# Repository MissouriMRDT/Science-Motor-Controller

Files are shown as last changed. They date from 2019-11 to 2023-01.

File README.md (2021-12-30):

# ScienceMotorController_Hardware
Hardware files for the Science Motor Controller (Science MOCO) board <br/>
The entire science system runs off of the 12V 40A auxillary buck from Powerboard. 
Science MOCO disctributes power to the rest of the science system (heater board and science sensors) in addition to driving brushed DC motors, servos, and solenoids.

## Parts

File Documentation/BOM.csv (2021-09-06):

Id | Designator | Package | Designation | Item Name | Part Number | Manufacturing Part Number | Vendor | Quantity | Cost Per Item | Cost | URL | Comments
1 | U7,U3,U4,U5,U6,U8 | MultiPowerSO_30 | VNH5019A_E | Motor Driver | 45AC7961 | VNH5019ATR-E | Newark | 6 | 7.51 | 46.02 | https://www.newark.com/stmicroelectronics/vnh5019atr-e/motor-driver-aec-q100-multipowerso/dp/45AC7961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
2 | Conn2,Conn1 | Anderson_3_Vertical_Side_by_Side | AndersonPP |  | 1335G1 |  |  | 2 |  | 0 | https://powerwerx.com/anderson-1335g1-printed-circuit-board-vertical
3 | D7,D10,D13,D16,D19,D26 | D_0603_1608Metric_Pad1.05x0.95mm_HandSolder | D_Zener_Small | Zener Diode | SDZT15R5.6CT-ND | SDZT15R5.6? | Digikey | 6 |  | 0 | https://www.digikey.com/en/products/detail/SDZT15R5.6/SDZT15R5.6CT-ND/5726746?itemSeq=346675758
4 | C3,C4,C5,C6,C7,C8 | C_0603_1608Metric_Pad1.05x0.95mm_HandSolder | 33nF | Capacitor | 1276-2044-1-ND | CL10B333KO8NNNC? | Digikey | 6 |  | 0 | https://www.digikey.com/en/products/detail/CL10B333KO8NNNC/1276-2044-1-ND/3890130?itemSeq=346676154
5 | R7,R8,R9,R10,R11,R12,R16,R17,R18,R19,R20,R21,R25,R26,R27,R28,R29,R30,R34,R35,R36,R37,R38,R39,R43,R44,R45,R46,R47,R48,R56,R57,R58,R59,R60,R61 | R_0603_1608Metric_Pad1.05x0.95mm_HandSolder | 1k | Resistor | RHM1.0KDCT-ND | ESR03EZPJ102? | Digikey | 36 | 0.1 | 3.6 | https://www.digikey.com/en/products/detail/rohm-semiconductor/ESR03EZPJ102/1762924
6 | R6,R15,R24,R33,R42,R55 | R_0603_1608Metric_Pad1.05x0.95mm_HandSolder | 10k | Resistor | RHM10KADCT-ND | ESR03EZPF1002? | Digikey | 6 | 0.12 | 0.72 | https://www.digikey.com/en/products/detail/rohm-semiconductor/ESR03EZPF1002/1983753
7 | Conn3,Conn4,Conn5,Conn6,Conn7,Conn12 | Anderson_2_Horizontal_Side_by_Side | AndersonPP |  | 1336G1 |  |  | 6 |  | 0 | https://powerwerx.com/anderson-1336g1-printed-circuit-board-horizontal
8 | Conn8,Conn9,Conn10,Conn11 | MOLEX_SL_02_Vertical | Molex_SL_02 | Connector | WM4800-ND | 0705430001? | Digikey | 4 | 0.74 | 2.96 | https://www.digikey.com/en/products/detail/molex/0705430001/114915?s=N4IgTCBcDaIOoFkAsAOADGgtAOQCIgF0BfIA
9 | Conn13,Conn14 | MOLEX_SL_03_Vertical | Molex_SL_03 | Connector | WM4801-ND | 0705430002? | Digikey | 2 | 0.74 | 1.48 | https://www.digikey.com/en/products/detail/molex/0705430002/114919?s=N4IgTCBcDaIOoFkAsAOADARgLQDkAiIAugL5A
10 | D6 | LED_0603_1608Metric_Pad1.05x0.95mm_HandSolder | Red LED | LED | 160-1447-1-ND | ?LTST-C191KRKT? | Digikey | 1 | 0.26 | 0.26 | https://www.digikey.com/en/products/detail/lite-on-inc/LTST-C191KRKT/386836
11 | D5 | LED_0603_1608Metric_Pad1.05x0.95mm_HandSolder | Yellow LED | LED | 160-1448-1-ND | ?LTST-C191KSKT? | Digikey | 1 | 0.28 | 0.28 | https://www.digikey.com/en/products/detail/lite-on-inc/LTST-C191KSKT/386838
12 | 12VL,3.3VL | LED_0603_1608Metric_Pad1.05x0.95mm_HandSolder | Green LED | LED | 160-1446-1-ND | LTST-C191KGKT | Digikey | 2 | 0.26 | 0.52 | https://www.digikey.com/en/products/detail/lite-on-inc/LTST-C191KGKT/386834
13 | D27,D28,D8,D9,D11,D12,D14,D15,D17,D18,D20,D21,D22,D23,D24,D25 | LED_0603_1608Metric_Pad1.05x0.95mm_HandSolder | Blue LED | LED | 160-1647-1-ND | ?LTST-C191TBKT? | Digikey | 16 | 0.33 | 5.28 | https://www.digikey.com/en/products/detail/lite-on-inc/LTST-C191TBKT/573587
14 | D1 | LED_0603_1608Metric_Pad1.05x0.95mm_HandSolder | Orange LED | LED | 160-1445-1-ND | ?LTST-C191KFKT? | Digikey | 1 | 0.24 | 0.24 | https://www.digikey.com/en/products/detail/lite-on-inc/LTST-C191KFKT/386832
15 | R1,R2 | R_0603_1608Metric_Pad1.05x0.95mm_HandSolder | 1.2k | Resistor | 311-1.2KDTR-ND | RT0603DRD071K2L? | Digikey | 2 | 0.17 | 0.34 | https://www.digikey.com/en/products/detail/yageo/RT0603DRD071K2L/1035462
16 | R4,R5,R51,R52,R53,R54,R3 | R_0603_1608Metric_Pad1.05x0.95mm_HandSolder | 330 | Resistor | 311-330DTR-ND | RT0603DRD07330RL? | Digikey | 7 | 0.17 | 1.19 | https://www.digikey.com/en/products/detail/yageo/RT0603DRD07330RL/1035528
17 | R13,R14,R22,R23,R31,R32,R40,R41,R49,R50,R62,R63 | R_0603_1608Metric_Pad1.05x0.95mm_HandSolder | 1.5k | Resistor | RHM1.5KDCT-ND | ESR03EZPJ152? | Digikey | 12 | 0.1 | 1.2 | https://www.digikey.com/product-detail/en/rohm-semiconductor/ESR03EZPJ152/RHM1.5KDCT-ND/1983780
18 | C1,C2 | C_0603_1608Metric_Pad1.05x0.95mm_HandSolder | 10uF | Capacitor | 1608-1357-1-ND | 0603J0160104KXT? | Digikey | 2 | 0.59 | 1.18 | https://www.digikey.com/en/products/detail/knowles-syfer/0603J0160104KXT/6282146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
19 | U1 | OKI_Horizontal | OKI | 3.3V OKI | 811-3014-ND | OKI-78SR-3.3/1.5-W36H-C | Digikey | 1 | 4.3 | 4.3 | https://www.digikey.com/product-detail/en/diodes-incorporated/AP1509-33SG-13/AP1509-33SGDICT-ND/1301652
20 | U2 | TM4C129E_Launchpad_FULL_THT_BOTTOM | TM4C129E_Launchpad | Tiva Launchpad | 296-44249-ND | EK-TM4C129EXL | Digikey | 1 | 29.99 | 29.99 | https://www.digikey.com/product-detail/en/texas-instruments/EK-TM4C129EXL/296-44249-ND/5764631

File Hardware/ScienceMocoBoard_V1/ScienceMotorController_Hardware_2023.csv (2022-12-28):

Source: | C:\Users\Brink\OneDrive\Documents\GitHub\ScienceMotorController_Hardware\Hardware\ScienceMocoBoard_V1\ScienceMotorController_Hardware_2023.kicad_sch
Date: | 12/28/2022 3:21:48 PM
Tool: | Eeschema (6.0.10)
Generator: | C:\Program Files\KiCad\6.0\bin\scripting\plugins/bom_csv_grouped_by_value.py
Component Count: | 182
Individual Components:
Item | Qty | Reference(s) | Value | LibPart | Footprint | Datasheet | MANUFACTURER | MAXIMUM_PACKAGE_HEIGHT | PARTREV | STANDARD
 |  | AbsEncode1 | Molex_SL_03 | MRDT_Connectors:Molex_SL_03 | MRDT_Connectors:MOLEX_SL_03_Vertical
 |  | AbsEncode2 | Molex_SL_03 | MRDT_Connectors:Molex_SL_03 | MRDT_Connectors:MOLEX_SL_03_Vertical
 |  | AbsEncode3 | Molex_SL_03 | MRDT_Connectors:Molex_SL_03 | MRDT_Connectors:MOLEX_SL_03_Vertical
 |  | AbsEncode4 | Molex_SL_03 | MRDT_Connectors:Molex_SL_03 | MRDT_Connectors:MOLEX_SL_03_Vertical
 |  | C1 | 1u | Device:C | Capacitor_SMD:C_0603_1608Metric | ~
 |  | C2 | 10u | Device:C_Small | Capacitor_SMD:C_0603_1608Metric | ~
 |  | C3 | 1u | Device:C | Capacitor_SMD:C_0603_1608Metric | ~
 |  | C4 | 1u | Device:C | Capacitor_SMD:C_0603_1608Metric | ~
 |  | C5 | 10u | Device:C_Small | Capacitor_SMD:C_0603_1608Metric | ~
 |  | C6 | 1u | Device:C | Capacitor_SMD:C_0603_1608Metric | ~
 |  | C7 | 1u | Device:C | Capacitor_SMD:C_0603_1608Metric | ~
 |  | C8 | 10u | Device:C_Small | Capacitor_SMD:C_0603_1608Metric | ~
 |  | C9 | 1u | Device:C | Capacitor_SMD:C_0603_1608Metric | ~
 |  | C10 | 1u | Device:C | Capacitor_SMD:C_0603_1608Metric | ~
 |  | C11 | 10u | Device:C_Small | Capacitor_SMD:C_0603_1608Metric | ~
 |  | C12 | 1u | Device:C | Capacitor_SMD:C_0603_1608Metric | ~
 |  | C13 | 0.1uF | Device:C | Capacitor_SMD:C_0603_1608Metric_Pad1.08x0.95mm_HandSolder | ~
 |  | Conn1 | Input | MRDT_Connectors:AndersonPP | MRDT_Connectors:Square_Anderson_2_H_Side_By_Side
 |  | Conn2 | Output1 | MRDT_Connectors:AndersonPP | MRDT_Connectors:Square_Anderson_2_H_Side_By_Side
 |  | Conn3 | Output2 | MRDT_Connectors:AndersonPP | MRDT_Connectors:Square_Anderson_2_H_Side_By_Side
 |  | Conn4 | AndersonPP | MRDT_Connectors:AndersonPP | MRDT_Connectors:Square_Anderson_2_H_Side_By_Side
 |  | Conn5 | AndersonPP | MRDT_Connectors:AndersonPP | MRDT_Connectors:Square_Anderson_2_H_Side_By_Side
 |  | Conn6 | AndersonPP | MRDT_Connectors:AndersonPP | MRDT_Connectors:Square_Anderson_2_H_Side_By_Side
 |  | Conn7 | AndersonPP | MRDT_Connectors:AndersonPP | MRDT_Connectors:Square_Anderson_2_H_Side_By_Side
 |  | D1 | Orange | Device:LED_Small | LED_SMD:LED_0603_1608Metric_Pad1.05x0.95mm_HandSolder | ~
 |  | D2 | GREEN | Device:LED_Small | LED_SMD:LED_0603_1608Metric_Pad1.05x0.95mm_HandSolder | ~
 |  | D3 | D_Small | Device:D_Small | LED_SMD:LED_0603_1608Metric_Pad1.05x0.95mm_HandSolder | ~
 |  | D4 | Orange | Device:LED_Small | LED_SMD:LED_0603_1608Metric_Pad1.05x0.95mm_HandSolder | ~
 |  | D5 | GREEN | Device:LED_Small | LED_SMD:LED_0603_1608Metric_Pad1.05x0.95mm_HandSolder | ~
 |  | D6 | D_Small | Device:D_Small | LED_SMD:LED_0603_1608Metric_Pad1.05x0.95mm_HandSolder | ~
 |  | D7 | YELLOW | Device:LED_Small | LED_SMD:LED_0603_1608Metric_Pad1.05x0.95mm_HandSolder | ~
 |  | D8 | YELLOW | Device:LED_Small | LED_SMD:LED_0603_1608Metric_Pad1.05x0.95mm_HandSolder | ~
 |  | D9 | YELLOW | Device:LED_Small | LED_SMD:LED_0603_1608Metric_Pad1.05x0.95mm_HandSolder | ~
 |  | D10 | YELLOW | Device:LED_Small | LED_SMD:LED_0603_1608Metric_Pad1.05x0.95mm_HandSolder | ~
 |  | D11 | D_Small | Device:D_Small | LED_SMD:LED_0603_1608Metric_Pad1.05x0.95mm_HandSolder | ~
 |  | D12 | Orange | Device:LED_Small | LED_SMD:LED_0603_1608Metric_Pad1.05x0.95mm_HandSolder | ~
 |  | D13 | D_Small | Device:D_Small | LED_SMD:LED_0603_1608Metric_Pad1.05x0.95mm_HandSolder | ~
 |  | D14 | Orange | Device:LED_Small | LED_SMD:LED_0603_1608Metric_Pad1.05x0.95mm_HandSolder | ~
 |  | D15 | Orange | Device:LED_Small | LED_SMD:LED_0603_1608Metric_Pad1.05x0.95mm_HandSolder | ~
 |  | D16 | D_Small | Device:D_Small | LED_SMD:LED_0603_1608Metric_Pad1.05x0.95mm_HandSolder | ~
 |  | D17 | Orange | Device:LED_Small | LED_SMD:LED_0603_1608Metric_Pad1.05x0.95mm_HandSolder | ~
 |  | D18 | D_Small | Device:D_Small | LED_SMD:LED_0603_1608Metric_Pad1.05x0.95mm_HandSolder | ~
 |  | D19 | D_Small | Device:D_Small | LED_SMD:LED_0603_1608Metric_Pad1.05x0.95mm_HandSolder | ~
 |  | D20 | Orange | Device:LED_Small | LED_SMD:LED_0603_1608Metric_Pad1.05x0.95mm_HandSolder | ~
 |  | D21 | D_Small | Device:D_Small | LED_SMD:LED_0603_1608Metric_Pad1.05x0.95mm_HandSolder | ~
 |  | D22 | Orange | Device:LED_Small | LED_SMD:LED_0603_1608Metric_Pad1.05x0.95mm_HandSolder | ~
 |  | D23 | YELLOW | Device:LED_Small | LED_SMD:LED_0603_1608Metric_Pad1.05x0.95mm_HandSolder | ~
 |  | D24 | YELLOW | Device:LED_Small | LED_SMD:LED_0603_1608Metric_Pad1.05x0.95mm_HandSolder | ~
 |  | D25 | YELLOW | Device:LED_Small | LED_SMD:LED_0603_1608Metric_Pad1.05x0.95mm_HandSolder | ~
 |  | D26 | YELLOW | Device:LED_Small | LED_SMD:LED_0603_1608Metric_Pad1.05x0.95mm_HandSolder | ~
 |  | D27 | YELLOW | Device:LED_Small | LED_SMD:LED_0603_1608Metric_Pad1.05x0.95mm_HandSolder | ~
 |  | D28 | YELLOW | Device:LED_Small | LED_SMD:LED_0603_1608Metric_Pad1.05x0.95mm_HandSolder | ~
 |  | D29 | YELLOW | Device:LED_Small | LED_SMD:LED_0603_1608Metric_Pad1.05x0.95mm_HandSolder | ~
 |  | D30 | YELLOW | Device:LED_Small | LED_SMD:LED_0603_1608Metric_Pad1.05x0.95mm_HandSolder | ~
 |  | D31 | YELLOW | Device:LED_Small | LED_SMD:LED_0603_1608Metric_Pad1.05x0.95mm_HandSolder | ~
 |  | D32 | Green | Device:LED_Small | LED_SMD:LED_0603_1608Metric_Pad1.05x0.95mm_HandSolder | ~
 |  | DY1 | LED | Device:LED | LED_SMD:LED_0603_1608Metric_Pad1.05x0.95mm_HandSolder | ~
 |  | DY2 | LED | Device:LED | LED_SMD:LED_0603_1608Metric_Pad1.05x0.95mm_HandSolder | ~
 |  | DY3 | LED | Device:LED | LED_SMD:LED_0603_1608Metric_Pad1.05x0.95mm_HandSolder | ~
 |  | DY4 | LED | Device:LED | LED_SMD:LED_0603_1608Metric_Pad1.05x0.95mm_HandSolder | ~
 |  | DY5 | LED | Device:LED | LED_SMD:LED_0603_1608Metric_Pad1.05x0.95mm_HandSolder | ~
 |  | DY6 | LED | Device:LED | LED_SMD:LED_0603_1608Metric_Pad1.05x0.95mm_HandSolder | ~
 |  | DY7 | LED | Device:LED | LED_SMD:LED_0603_1608Metric_Pad1.05x0.95mm_HandSolder | ~
 |  | DY8 | LED | Device:LED | LED_SMD:LED_0603_1608Metric_Pad1.05x0.95mm_HandSolder | ~
 |  | DY9 | LED | Device:LED | LED_SMD:LED_0603_1608Metric_Pad1.05x0.95mm_HandSolder | ~
 |  | DY10 | LED | Device:LED | LED_SMD:LED_0603_1608Metric_Pad1.05x0.95mm_HandSolder | ~
 |  | DY11 | LED | Device:LED | LED_SMD:LED_0603_1608Metric_Pad1.05x0.95mm_HandSolder | ~
 |  | DY12 | LED | Device:LED | LED_SMD:LED_0603_1608Metric_Pad1.05x0.95mm_HandSolder | ~
 |  | J1 | RJ45_LED_Shielded | Connector:RJ45_LED_Shielded | MRDT_Connectors:RJ45_Teensy | ~
 |  | J2 | Conn_02x03_Counter_Clockwise | Connector_Generic:Conn_02x03_Counter_Clockwise | Connector_PinHeader_2.00mm:PinHeader_2x03_P2.00mm_Vertical | ~
 |  | LimSwitch1 | Molex_SL_02 | MRDT_Connectors:Molex_SL_02 | MRDT_Connectors:MOLEX_SL_02_Vertical
 |  | LimSwitch2 | Molex_SL_02 | MRDT_Connectors:Molex_SL_02 | MRDT_Connectors:MOLEX_SL_02_Vertical
 |  | LimSwitch3 | Molex_SL_02 | MRDT_Connectors:Molex_SL_02 | MRDT_Connectors:MOLEX_SL_02_Vertical
 |  | LimSwitch4 | Molex_SL_02 | MRDT_Connectors:Molex_SL_02 | MRDT_Connectors:MOLEX_SL_02_Vertical
 |  | LimSwitch5 | Molex_SL_02 | MRDT_Connectors:Molex_SL_02 | MRDT_Connectors:MOLEX_SL_02_Vertical
 |  | LimSwitch6 | Molex_SL_02 | MRDT_Connectors:Molex_SL_02 | MRDT_Connectors:MOLEX_SL_02_Vertical
 |  | LimSwitch7 | Molex_SL_02 | MRDT_Connectors:Molex_SL_02 | MRDT_Connectors:MOLEX_SL_02_Vertical
 |  | LimSwitch8 | Molex_SL_02 | MRDT_Connectors:Molex_SL_02 | MRDT_Connectors:MOLEX_SL_02_Vertical
 |  | LimSwitch9 | Molex_SL_02 | MRDT_Connectors:Molex_SL_02 | MRDT_Connectors:MOLEX_SL_02_Vertical
 |  | Q1 | SI4156DY | Transistor_FET:FDS2734 | Package_SO:SOIC-8_3.9x4.9mm_P1.27mm | https://www.onsemi.com/pdf/datasheet/fds8896-d.pdf
 |  | Q2 | SI4156DY | Transistor_FET:FDS2734 | Package_SO:SOIC-8_3.9x4.9mm_P1.27mm | https://www.onsemi.com/pdf/datasheet/fds8896-d.pdf
 |  | Q3 | SI4156DY | Transistor_FET:FDS2734 | Package_SO:SOIC-8_3.9x4.9mm_P1.27mm | https://www.onsemi.com/pdf/datasheet/fds8896-d.pdf
 |  | Q4 | SI4156DY | Transistor_FET:FDS2734 | Package_SO:SOIC-8_3.9x4.9mm_P1.27mm | https://www.onsemi.com/pdf/datasheet/fds8896-d.pdf
 |  | Q5 | SI4156DY | Transistor_FET:FDS2734 | Package_SO:SOIC-8_3.9x4.9mm_P1.27mm | https://www.onsemi.com/pdf/datasheet/fds8896-d.pdf
 |  | Q6 | SI4156DY | Transistor_FET:FDS2734 | Package_SO:SOIC-8_3.9x4.9mm_P1.27mm | https://www.onsemi.com/pdf/datasheet/fds8896-d.pdf
 |  | Q7 | SI4156DY | Transistor_FET:FDS2734 | Package_SO:SOIC-8_3.9x4.9mm_P1.27mm | https://www.onsemi.com/pdf/datasheet/fds8896-d.pdf
 |  | Q8 | SI4156DY | Transistor_FET:FDS2734 | Package_SO:SOIC-8_3.9x4.9mm_P1.27mm | https://www.onsemi.com/pdf/datasheet/fds8896-d.pdf
 |  | Q9 | SI4156DY | Transistor_FET:FDS2734 | Package_SO:SOIC-8_3.9x4.9mm_P1.27mm | https://www.onsemi.com/pdf/datasheet/fds8896-d.pdf
 |  | Q10 | SI4156DY | Transistor_FET:FDS2734 | Package_SO:SOIC-8_3.9x4.9mm_P1.27mm | https://www.onsemi.com/pdf/datasheet/fds8896-d.pdf
 |  | Q11 | SI4156DY | Transistor_FET:FDS2734 | Package_SO:SOIC-8_3.9x4.9mm_P1.27mm | https://www.onsemi.com/pdf/datasheet/fds8896-d.pdf
 |  | Q12 | SI4156DY | Transistor_FET:FDS2734 | Package_SO:SOIC-8_3.9x4.9mm_P1.27mm | https://www.onsemi.com/pdf/datasheet/fds8896-d.pdf
 |  | Q13 | SI4156DY | Transistor_FET:FDS2734 | Package_SO:SOIC-8_3.9x4.9mm_P1.27mm | https://www.onsemi.com/pdf/datasheet/fds8896-d.pdf
 |  | Q14 | SI4156DY | Transistor_FET:FDS2734 | Package_SO:SOIC-8_3.9x4.9mm_P1.27mm | https://www.onsemi.com/pdf/datasheet/fds8896-d.pdf
 |  | Q15 | SI4156DY | Transistor_FET:FDS2734 | Package_SO:SOIC-8_3.9x4.9mm_P1.27mm | https://www.onsemi.com/pdf/datasheet/fds8896-d.pdf
 |  | Q16 | SI4156DY | Transistor_FET:FDS2734 | Package_SO:SOIC-8_3.9x4.9mm_P1.27mm | https://www.onsemi.com/pdf/datasheet/fds8896-d.pdf
 |  | R1 | 120 | Device:R_Small | Resistor_SMD:R_0603_1608Metric_Pad0.98x0.95mm_HandSolder | ~
 |  | R2 | 1k | Device:R | Resistor_SMD:R_0603_1608Metric_Pad0.98x0.95mm_HandSolder | ~
 |  | R3 | 100 | Device:R | Resistor_SMD:R_0603_1608Metric_Pad0.98x0.95mm_HandSolder | ~
 |  | R4 | 100 | Device:R | Resistor_SMD:R_0603_1608Metric_Pad0.98x0.95mm_HandSolder | ~
 |  | R5 | 120 | Device:R_Small | Resistor_SMD:R_0603_1608Metric_Pad0.98x0.95mm_HandSolder | ~
 |  | R6 | 300 | Device:R | Resistor_SMD:R_0603_1608Metric_Pad0.98x0.95mm_HandSolder | ~
 |  | R7 | 100 | Device:R | Resistor_SMD:R_0603_1608Metric_Pad0.98x0.95mm_HandSolder | ~
 |  | R8 | 100 | Device:R | Resistor_SMD:R_0603_1608Metric_Pad0.98x0.95mm_HandSolder | ~
 |  | R9 | 100 | Device:R | Resistor_SMD:R_0603_1608Metric_Pad0.98x0.95mm_HandSolder | ~
 |  | R10 | 100 | Device:R | Resistor_SMD:R_0603_1608Metric_Pad0.98x0.95mm_HandSolder | ~
 |  | R11 | 100 | Device:R | Resistor_SMD:R_0603_1608Metric_Pad0.98x0.95mm_HandSolder | ~
 |  | R12 | 100 | Device:R | Resistor_SMD:R_0603_1608Metric_Pad0.98x0.95mm_HandSolder | ~
 |  | R13 | 100 | Device:R | Resistor_SMD:R_0603_1608Metric_Pad0.98x0.95mm_HandSolder | ~
 |  | R14 | 100 | Device:R | Resistor_SMD:R_0603_1608Metric_Pad0.98x0.95mm_HandSolder | ~
 |  | R15 | 100 | Device:R | Resistor_SMD:R_0603_1608Metric_Pad0.98x0.95mm_HandSolder | ~
 |  | R16 | 100 | Device:R | Resistor_SMD:R_0603_1608Metric_Pad0.98x0.95mm_HandSolder | ~
 |  | R17 | 120 | Device:R | Resistor_SMD:R_0603_1608Metric_Pad0.98x0.95mm_HandSolder | ~
 |  | R18 | 120 | Device:R | Resistor_SMD:R_0603_1608Metric_Pad0.98x0.95mm_HandSolder | ~
 |  | R19 | 120 | Device:R | Resistor_SMD:R_0603_1608Metric_Pad0.98x0.95mm_HandSolder | ~
 |  | R20 | 120 | Device:R | Resistor_SMD:R_0603_1608Metric_Pad0.98x0.95mm_HandSolder | ~
 |  | R21 | 120 | Device:R_Small | Resistor_SMD:R_0603_1608Metric_Pad0.98x0.95mm_HandSolder | ~
 |  | R22 | 100 | Device:R | Resistor_SMD:R_0603_1608Metric_Pad0.98x0.95mm_HandSolder | ~
 |  | R23 | 100 | Device:R | Resistor_SMD:R_0603_1608Metric_Pad0.98x0.95mm_HandSolder | ~
 |  | R24 | 100 | Device:R | Resistor_SMD:R_0603_1608Metric_Pad0.98x0.95mm_HandSolder | ~
 |  | R25 | 100 | Device:R | Resistor_SMD:R_0603_1608Metric_Pad0.98x0.95mm_HandSolder | ~
 |  | R26 | 100 | Device:R | Resistor_SMD:R_0603_1608Metric_Pad0.98x0.95mm_HandSolder | ~
 |  | R27 | 100 | Device:R | Resistor_SMD:R_0603_1608Metric_Pad0.98x0.95mm_HandSolder | ~
 |  | R28 | 120 | Device:R_Small | Resistor_SMD:R_0603_1608Metric_Pad0.98x0.95mm_HandSolder | ~
 |  | R29 | 120 | Device:R_Small | Resistor_SMD:R_0603_1608Metric_Pad0.98x0.95mm_HandSolder | ~
 |  | R30 | 100 | Device:R | Resistor_SMD:R_0603_1608Metric_Pad0.98x0.95mm_HandSolder | ~
 |  | R31 | 100 | Device:R | Resistor_SMD:R_0603_1608Metric_Pad0.98x0.95mm_HandSolder | ~
 |  | R32 | 120 | Device:R_Small | Resistor_SMD:R_0603_1608Metric_Pad0.98x0.95mm_HandSolder | ~
 |  | R33 | 100 | Device:R | Resistor_SMD:R_0603_1608Metric_Pad0.98x0.95mm_HandSolder | ~
 |  | R34 | 100 | Device:R | Resistor_SMD:R_0603_1608Metric_Pad0.98x0.95mm_HandSolder | ~
 |  | R35 | 100 | Device:R | Resistor_SMD:R_0603_1608Metric_Pad0.98x0.95mm_HandSolder | ~
 |  | R36 | 100 | Device:R | Resistor_SMD:R_0603_1608Metric_Pad0.98x0.95mm_HandSolder | ~
 |  | R37 | 100 | Device:R | Resistor_SMD:R_0603_1608Metric_Pad0.98x0.95mm_HandSolder | ~
 |  | R38 | 100 | Device:R | Resistor_SMD:R_0603_1608Metric_Pad0.98x0.95mm_HandSolder | ~
 |  | R39 | 120 | Device:R_Small | Resistor_SMD:R_0603_1608Metric_Pad0.98x0.95mm_HandSolder | ~
 |  | R40 | 100 | Device:R | Resistor_SMD:R_0603_1608Metric_Pad0.98x0.95mm_HandSolder | ~
 |  | R41 | 100 | Device:R | Resistor_SMD:R_0603_1608Metric_Pad0.98x0.95mm_HandSolder | ~
 |  | R42 | 120 | Device:R_Small | Resistor_SMD:R_0603_1608Metric_Pad0.98x0.95mm_HandSolder | ~
 |  | R43 | 120 | Device:R | Resistor_SMD:R_0603_1608Metric_Pad0.98x0.95mm_HandSolder | ~
 |  | R44 | 120 | Device:R | Resistor_SMD:R_0603_1608Metric_Pad0.98x0.95mm_HandSolder | ~
 |  | R45 | 120 | Device:R | Resistor_SMD:R_0603_1608Metric_Pad0.98x0.95mm_HandSolder | ~
 |  | R46 | 120 | Device:R | Resistor_SMD:R_0603_1608Metric_Pad0.98x0.95mm_HandSolder | ~
 |  | R47 | 120 | Device:R | Resistor_SMD:R_0603_1608Metric_Pad0.98x0.95mm_HandSolder | ~
 |  | R48 | 120 | Device:R | Resistor_SMD:R_0603_1608Metric_Pad0.98x0.95mm_HandSolder | ~
 |  | R49 | 120 | Device:R | Resistor_SMD:R_0603_1608Metric_Pad0.98x0.95mm_HandSolder | ~
 |  | R50 | 120 | Device:R | Resistor_SMD:R_0603_1608Metric_Pad0.98x0.95mm_HandSolder | ~
 |  | R51 | 120 | Device:R | Resistor_SMD:R_0603_1608Metric_Pad0.98x0.95mm_HandSolder | ~
 |  | R52 | 120 | Device:R | Resistor_SMD:R_0603_1608Metric_Pad0.98x0.95mm_HandSolder | ~
 |  | Servo1 | Molex_SL_03 | MRDT_Connectors:Molex_SL_03 | MRDT_Connectors:MOLEX_SL_03_Vertical
 |  | Servo2 | Molex_SL_03 | MRDT_Connectors:Molex_SL_03 | MRDT_Connectors:MOLEX_SL_03_Vertical
 |  | Servo3 | Molex_SL_03 | MRDT_Connectors:Molex_SL_03 | MRDT_Connectors:MOLEX_SL_03_Vertical
 |  | Servo4 | Molex_SL_03 | MRDT_Connectors:Molex_SL_03 | MRDT_Connectors:MOLEX_SL_03_Vertical
 |  | Servo5 | Molex_SL_03 | MRDT_Connectors:Molex_SL_03 | MRDT_Connectors:MOLEX_SL_03_Vertical
 |  | Servo6 | Molex_SL_03 | MRDT_Connectors:Molex_SL_03 | MRDT_Connectors:MOLEX_SL_03_Vertical
 |  | SW1 | SW_Push | Switch:SW_Push | Button_Switch_SMD:SW_SPST_EVPBF | ~
 |  | SW2 | SW_Push | Switch:SW_Push | Button_Switch_SMD:SW_SPST_EVPBF | ~
 |  | SW3 | SW_Push | Switch:SW_Push | Button_Switch_SMD:SW_SPST_EVPBF | ~
 |  | SW4 | SW_Push | Switch:SW_Push | Button_Switch_SMD:SW_SPST_EVPBF | ~
 |  | SW5 | SW_Push | Switch:SW_Push | Button_Switch_SMD:SW_SPST_EVPBF | ~
 |  | SW6 | SW_Push | Switch:SW_Push | Button_Switch_SMD:SW_SPST_EVPBF | ~
 |  | SW7 | SW_Push | Switch:SW_Push | Button_Switch_SMD:SW_SPST_EVPBF | ~
 |  | SW8 | SW_Push | Switch:SW_Push | Button_Switch_SMD:SW_SPST_EVPBF | ~
 |  | SW9 | SW_Push | Switch:SW_Push | Button_Switch_SMD:SW_SPST_EVPBF | ~
 |  | SW10 | SW_Push | Switch:SW_Push | Button_Switch_SMD:SW_SPST_EVPBF | ~
 |  | SW11 | SW_DPDT_x2 | Switch:SW_DPDT_x2 | Button_Switch_THT:SW_Slide_1P2T_CK_OS102011MS2Q | ~
 |  | U1 | 74LVC2G04 | 74xGxx:74LVC2G04 | Package_TO_SOT_SMD:SOT-23-6_Handsoldering | http://www.ti.com/lit/sg/scyt129e/scyt129e.pdf
 |  | U2 | IRS2005S | Driver_FET:IRS2005S | Package_SO:SOIC-8_3.9x4.9mm_P1.27mm | https://www.infineon.com/dgdl/Infineon-IRS2005S-DS-v02_00-EN.pdf?fileId=5546d462533600a4015364c4246229e1
 |  | U3 | TSR_1-2450 | Regulator_Switching:TSR_1-2450 | Converter_DCDC:Converter_DCDC_TRACO_TSR-1_THT | http://www.tracopower.com/products/tsr1.pdf
 |  | U4 | 74LVC2G04 | 74xGxx:74LVC2G04 | Package_TO_SOT_SMD:SOT-23-6_Handsoldering | http://www.ti.com/lit/sg/scyt129e/scyt129e.pdf
 |  | U5 | IRS2005S | Driver_FET:IRS2005S | Package_SO:SOIC-8_3.9x4.9mm_P1.27mm | https://www.infineon.com/dgdl/Infineon-IRS2005S-DS-v02_00-EN.pdf?fileId=5546d462533600a4015364c4246229e1
 |  | U6 | IRS2005S | Driver_FET:IRS2005S | Package_SO:SOIC-8_3.9x4.9mm_P1.27mm | https://www.infineon.com/dgdl/Infineon-IRS2005S-DS-v02_00-EN.pdf?fileId=5546d462533600a4015364c4246229e1
 |  | U7 | IRS2005S | Driver_FET:IRS2005S | Package_SO:SOIC-8_3.9x4.9mm_P1.27mm | https://www.infineon.com/dgdl/Infineon-IRS2005S-DS-v02_00-EN.pdf?fileId=5546d462533600a4015364c4246229e1
 |  | U8 | 74LVC2G04 | 74xGxx:74LVC2G04 | Package_TO_SOT_SMD:SOT-23-6_Handsoldering | http://www.ti.com/lit/sg/scyt129e/scyt129e.pdf
 |  | U9 | IRS2005S | Driver_FET:IRS2005S | Package_SO:SOIC-8_3.9x4.9mm_P1.27mm | https://www.infineon.com/dgdl/Infineon-IRS2005S-DS-v02_00-EN.pdf?fileId=5546d462533600a4015364c4246229e1
 |  | U10 | 74LVC2G04 | 74xGxx:74LVC2G04 | Package_TO_SOT_SMD:SOT-23-6_Handsoldering | http://www.ti.com/lit/sg/scyt129e/scyt129e.pdf
 |  | U11 | IRS2005S | Driver_FET:IRS2005S | Package_SO:SOIC-8_3.9x4.9mm_P1.27mm | https://www.infineon.com/dgdl/Infineon-IRS2005S-DS-v02_00-EN.pdf?fileId=5546d462533600a4015364c4246229e1
 |  | U12 | IRS2005S | Driver_FET:IRS2005S | Package_SO:SOIC-8_3.9x4.9mm_P1.27mm | https://www.infineon.com/dgdl/Infineon-IRS2005S-DS-v02_00-EN.pdf?fileId=5546d462533600a4015364c4246229e1
 |  | U13 | Teensy4.1_DEV-16771 | MRDT_Shields:Teensy4.1_DEV-16771 | MRDT_Shields:Teensy_4_1 |  | SparkFun Electronics | 4.07mm | 4.1 | Manufacturer recommendations
 |  | U14 | IRS2005S | Driver_FET:IRS2005S | Package_SO:SOIC-8_3.9x4.9mm_P1.27mm | https://www.infineon.com/dgdl/Infineon-IRS2005S-DS-v02_00-EN.pdf?fileId=5546d462533600a4015364c4246229e1
 |  | V1 | Via | MRDT_Drill_Holes:Via | MRDT_Drill_Holes:4_40_Hole_Corner
 |  | V2 | Via | MRDT_Drill_Holes:Via | MRDT_Drill_Holes:4_40_Hole_Corner
 |  | V3 | Via | MRDT_Drill_Holes:Via | MRDT_Drill_Holes:4_40_Hole_Corner
 |  | V4 | Via | MRDT_Drill_Holes:Via | MRDT_Drill_Holes:4_40_Hole_Corner
Collated Components:
Item | Qty | Reference(s) | Value | LibPart | Footprint | Datasheet | MANUFACTURER | MAXIMUM_PACKAGE_HEIGHT | PARTREV | STANDARD
1 | 10 | AbsEncode1, AbsEncode2, AbsEncode3, AbsEncode4, Servo1, Servo2, Servo3, Servo4, Servo5, Servo6 | Molex_SL_03 | MRDT_Connectors:Molex_SL_03 | MRDT_Connectors:MOLEX_SL_03_Vertical
2 | 8 | C1, C3, C4, C6, C7, C9, C10, C12 | 1u | Device:C | Capacitor_SMD:C_0603_1608Metric | ~
3 | 4 | C2, C5, C8, C11 | 10u | Device:C_Small | Capacitor_SMD:C_0603_1608Metric | ~
4 | 1 | C13 | 0.1uF | Device:C | Capacitor_SMD:C_0603_1608Metric_Pad1.08x0.95mm_HandSolder | ~
5 | 1 | Conn1 | Input | MRDT_Connectors:AndersonPP | MRDT_Connectors:Square_Anderson_2_H_Side_By_Side
6 | 1 | Conn2 | Output1 | MRDT_Connectors:AndersonPP | MRDT_Connectors:Square_Anderson_2_H_Side_By_Side
7 | 1 | Conn3 | Output2 | MRDT_Connectors:AndersonPP | MRDT_Connectors:Square_Anderson_2_H_Side_By_Side
8 | 4 | Conn4, Conn5, Conn6, Conn7 | AndersonPP | MRDT_Connectors:AndersonPP | MRDT_Connectors:Square_Anderson_2_H_Side_By_Side
9 | 8 | D1, D4, D12, D14, D15, D17, D20, D22 | Orange | Device:LED_Small | LED_SMD:LED_0603_1608Metric_Pad1.05x0.95mm_HandSolder | ~
10 | 2 | D2, D5 | GREEN | Device:LED_Small | LED_SMD:LED_0603_1608Metric_Pad1.05x0.95mm_HandSolder | ~
11 | 8 | D3, D6, D11, D13, D16, D18, D19, D21 | D_Small | Device:D_Small | LED_SMD:LED_0603_1608Metric_Pad1.05x0.95mm_HandSolder | ~
12 | 13 | D7, D8, D9, D10, D23, D24, D25, D26, D27, D28, D29, D30, D31 | YELLOW | Device:LED_Small | LED_SMD:LED_0603_1608Metric_Pad1.05x0.95mm_HandSolder | ~
13 | 1 | D32 | Green | Device:LED_Small | LED_SMD:LED_0603_1608Metric_Pad1.05x0.95mm_HandSolder | ~
14 | 12 | DY1, DY2, DY3, DY4, DY5, DY6, DY7, DY8, DY9, DY10, DY11, DY12 | LED | Device:LED | LED_SMD:LED_0603_1608Metric_Pad1.05x0.95mm_HandSolder | ~
15 | 1 | J1 | RJ45_LED_Shielded | Connector:RJ45_LED_Shielded | MRDT_Connectors:RJ45_Teensy | ~
16 | 1 | J2 | Conn_02x03_Counter_Clockwise | Connector_Generic:Conn_02x03_Counter_Clockwise | Connector_PinHeader_2.00mm:PinHeader_2x03_P2.00mm_Vertical | ~
17 | 9 | LimSwitch1, LimSwitch2, LimSwitch3, LimSwitch4, LimSwitch5, LimSwitch6, LimSwitch7, LimSwitch8, LimSwitch9 | Molex_SL_02 | MRDT_Connectors:Molex_SL_02 | MRDT_Connectors:MOLEX_SL_02_Vertical
18 | 16 | Q1, Q2, Q3, Q4, Q5, Q6, Q7, Q8, Q9, Q10, Q11, Q12, Q13, Q14, Q15, Q16 | SI4156DY | Transistor_FET:FDS2734 | Package_SO:SOIC-8_3.9x4.9mm_P1.27mm | https://www.onsemi.com/pdf/datasheet/fds8896-d.pdf
19 | 8 | R1, R5, R21, R28, R29, R32, R39, R42 | 120 | Device:R_Small | Resistor_SMD:R_0603_1608Metric_Pad0.98x0.95mm_HandSolder | ~
20 | 1 | R2 | 1k | Device:R | Resistor_SMD:R_0603_1608Metric_Pad0.98x0.95mm_HandSolder | ~
21 | 28 | R3, R4, R7, R8, R9, R10, R11, R12, R13, R14, R15, R16, R22, R23, R24, R25, R26, R27, R30, R31, R33, R34, R35, R36, R37, R38, R40, R41 | 100 | Device:R | Resistor_SMD:R_0603_1608Metric_Pad0.98x0.95mm_HandSolder | ~
22 | 1 | R6 | 300 | Device:R | Resistor_SMD:R_0603_1608Metric_Pad0.98x0.95mm_HandSolder | ~
23 | 14 | R17, R18, R19, R20, R43, R44, R45, R46, R47, R48, R49, R50, R51, R52 | 120 | Device:R | Resistor_SMD:R_0603_1608Metric_Pad0.98x0.95mm_HandSolder | ~
24 | 10 | SW1, SW2, SW3, SW4, SW5, SW6, SW7, SW8, SW9, SW10 | SW_Push | Switch:SW_Push | Button_Switch_SMD:SW_SPST_EVPBF | ~
25 | 1 | SW11 | SW_DPDT_x2 | Switch:SW_DPDT_x2 | Button_Switch_THT:SW_Slide_1P2T_CK_OS102011MS2Q | ~
26 | 4 | U1, U4, U8, U10 | 74LVC2G04 | 74xGxx:74LVC2G04 | Package_TO_SOT_SMD:SOT-23-6_Handsoldering | http://www.ti.com/lit/sg/scyt129e/scyt129e.pdf
27 | 8 | U2, U5, U6, U7, U9, U11, U12, U14 | IRS2005S | Driver_FET:IRS2005S | Package_SO:SOIC-8_3.9x4.9mm_P1.27mm | https://www.infineon.com/dgdl/Infineon-IRS2005S-DS-v02_00-EN.pdf?fileId=5546d462533600a4015364c4246229e1
28 | 1 | U3 | TSR_1-2450 | Regulator_Switching:TSR_1-2450 | Converter_DCDC:Converter_DCDC_TRACO_TSR-1_THT | http://www.tracopower.com/products/tsr1.pdf
29 | 1 | U13 | Teensy4.1_DEV-16771 | MRDT_Shields:Teensy4.1_DEV-16771 | MRDT_Shields:Teensy_4_1 |  | SparkFun Electronics | 4.07mm | 4.1 | Manufacturer recommendations
30 | 4 | V1, V2, V3, V4 | Via | MRDT_Drill_Holes:Via | MRDT_Drill_Holes:4_40_Hole_Corner

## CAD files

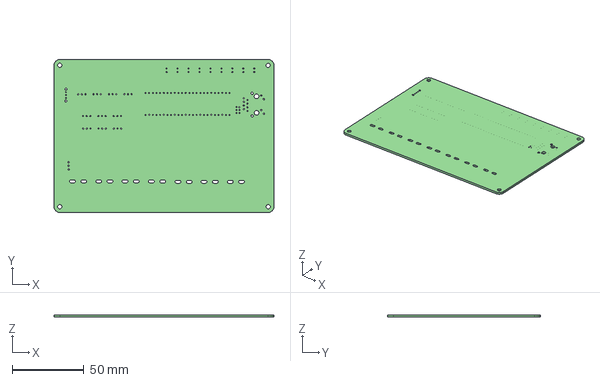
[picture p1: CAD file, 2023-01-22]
Documentation/ScienceMotorController.step
153.0 x 106.4 x 1.60 mm

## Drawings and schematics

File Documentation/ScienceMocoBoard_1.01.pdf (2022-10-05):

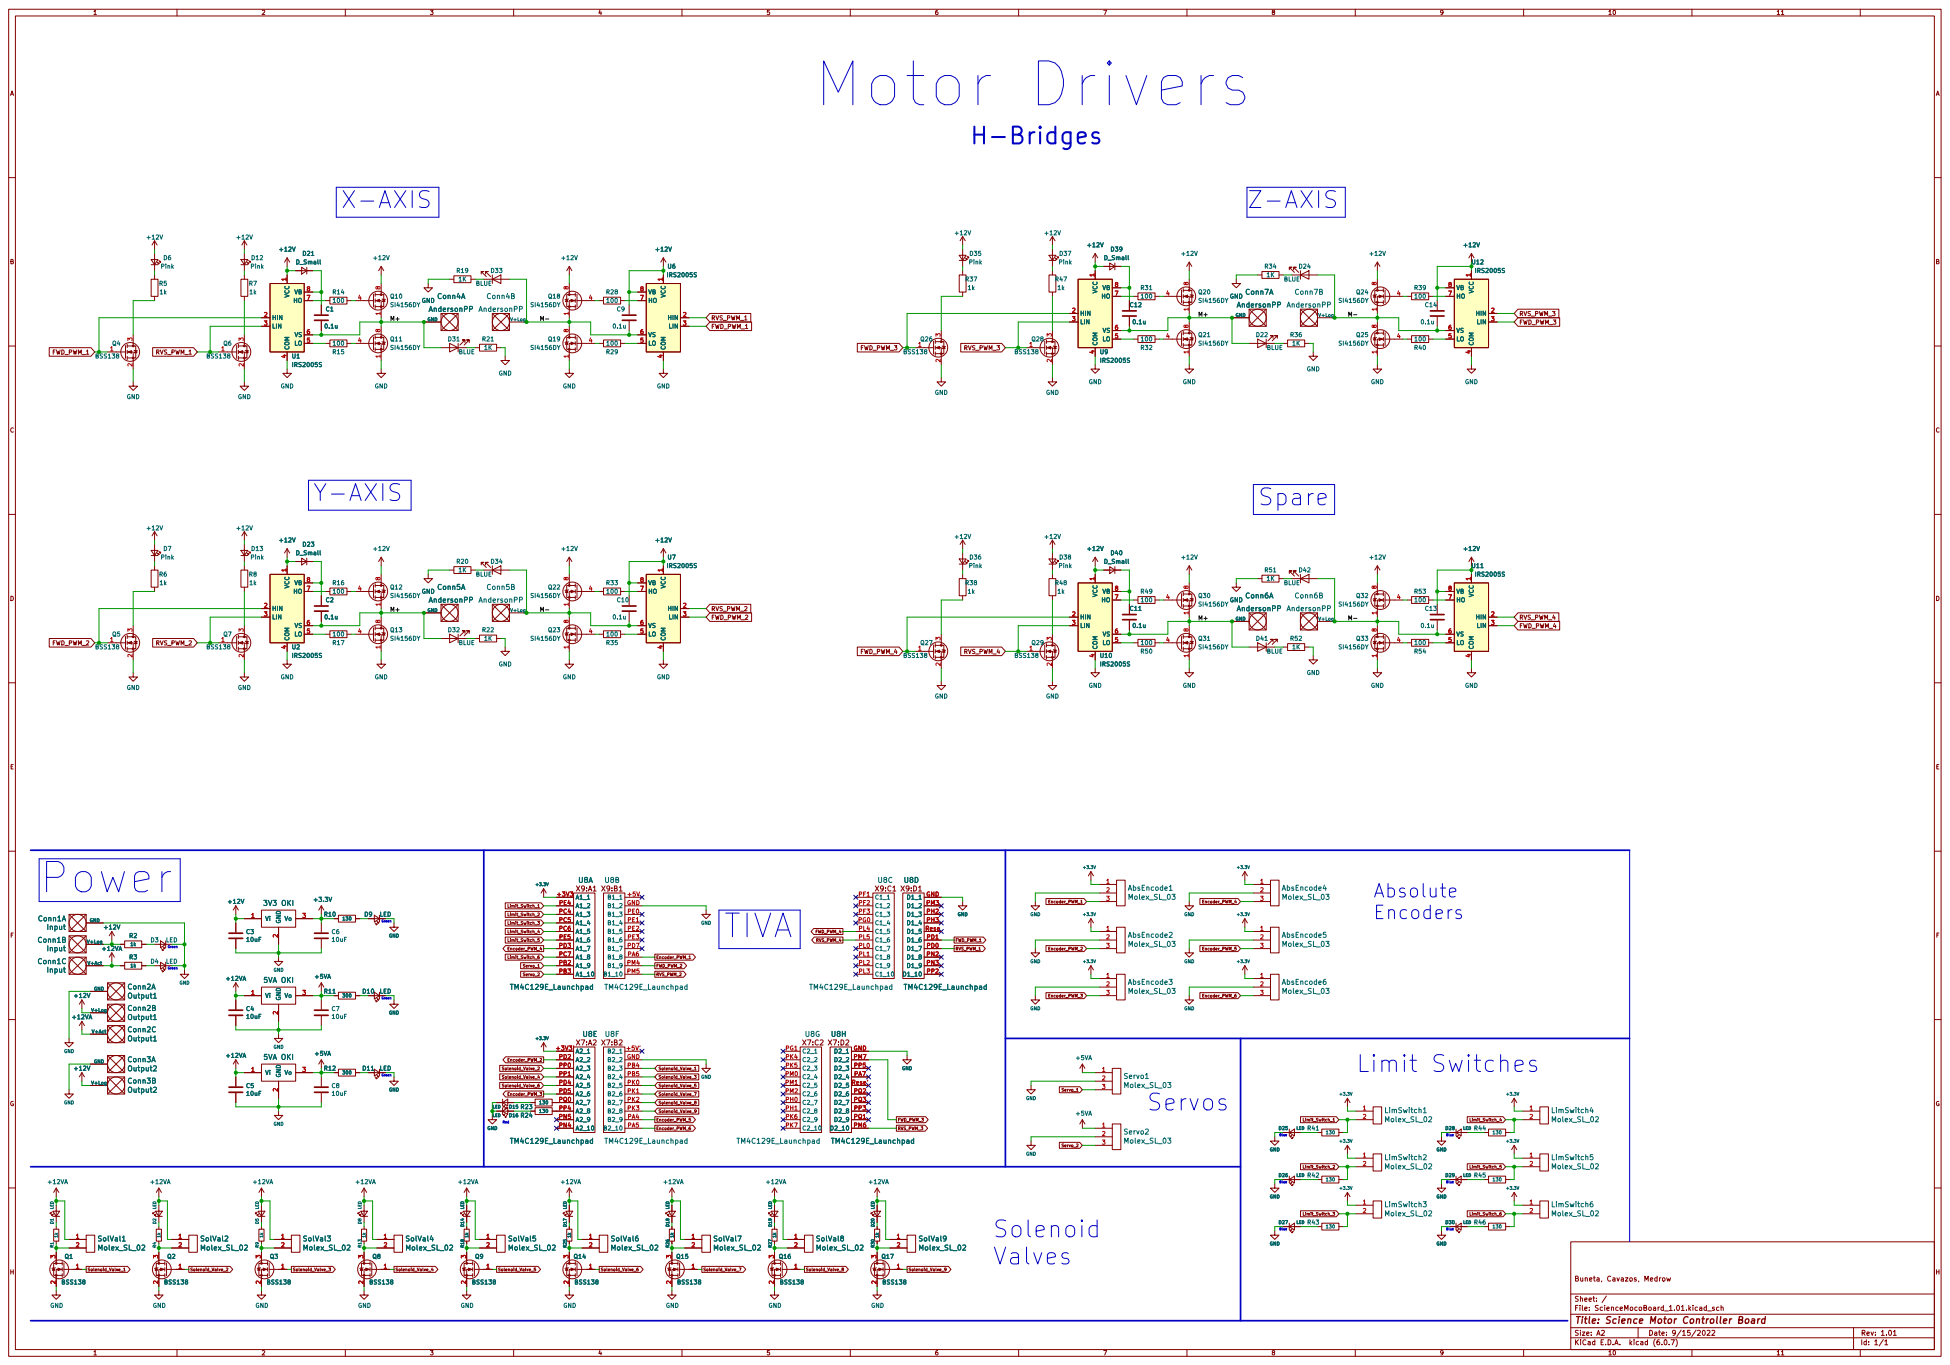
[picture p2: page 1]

Blue Blue Blue Servos

File: ScienceMocoBoard_1.01.kicad_sch Sheet: / Buneta, Cavazos, Medrow

Id: 1/1 Title: Science Motor Controller Board

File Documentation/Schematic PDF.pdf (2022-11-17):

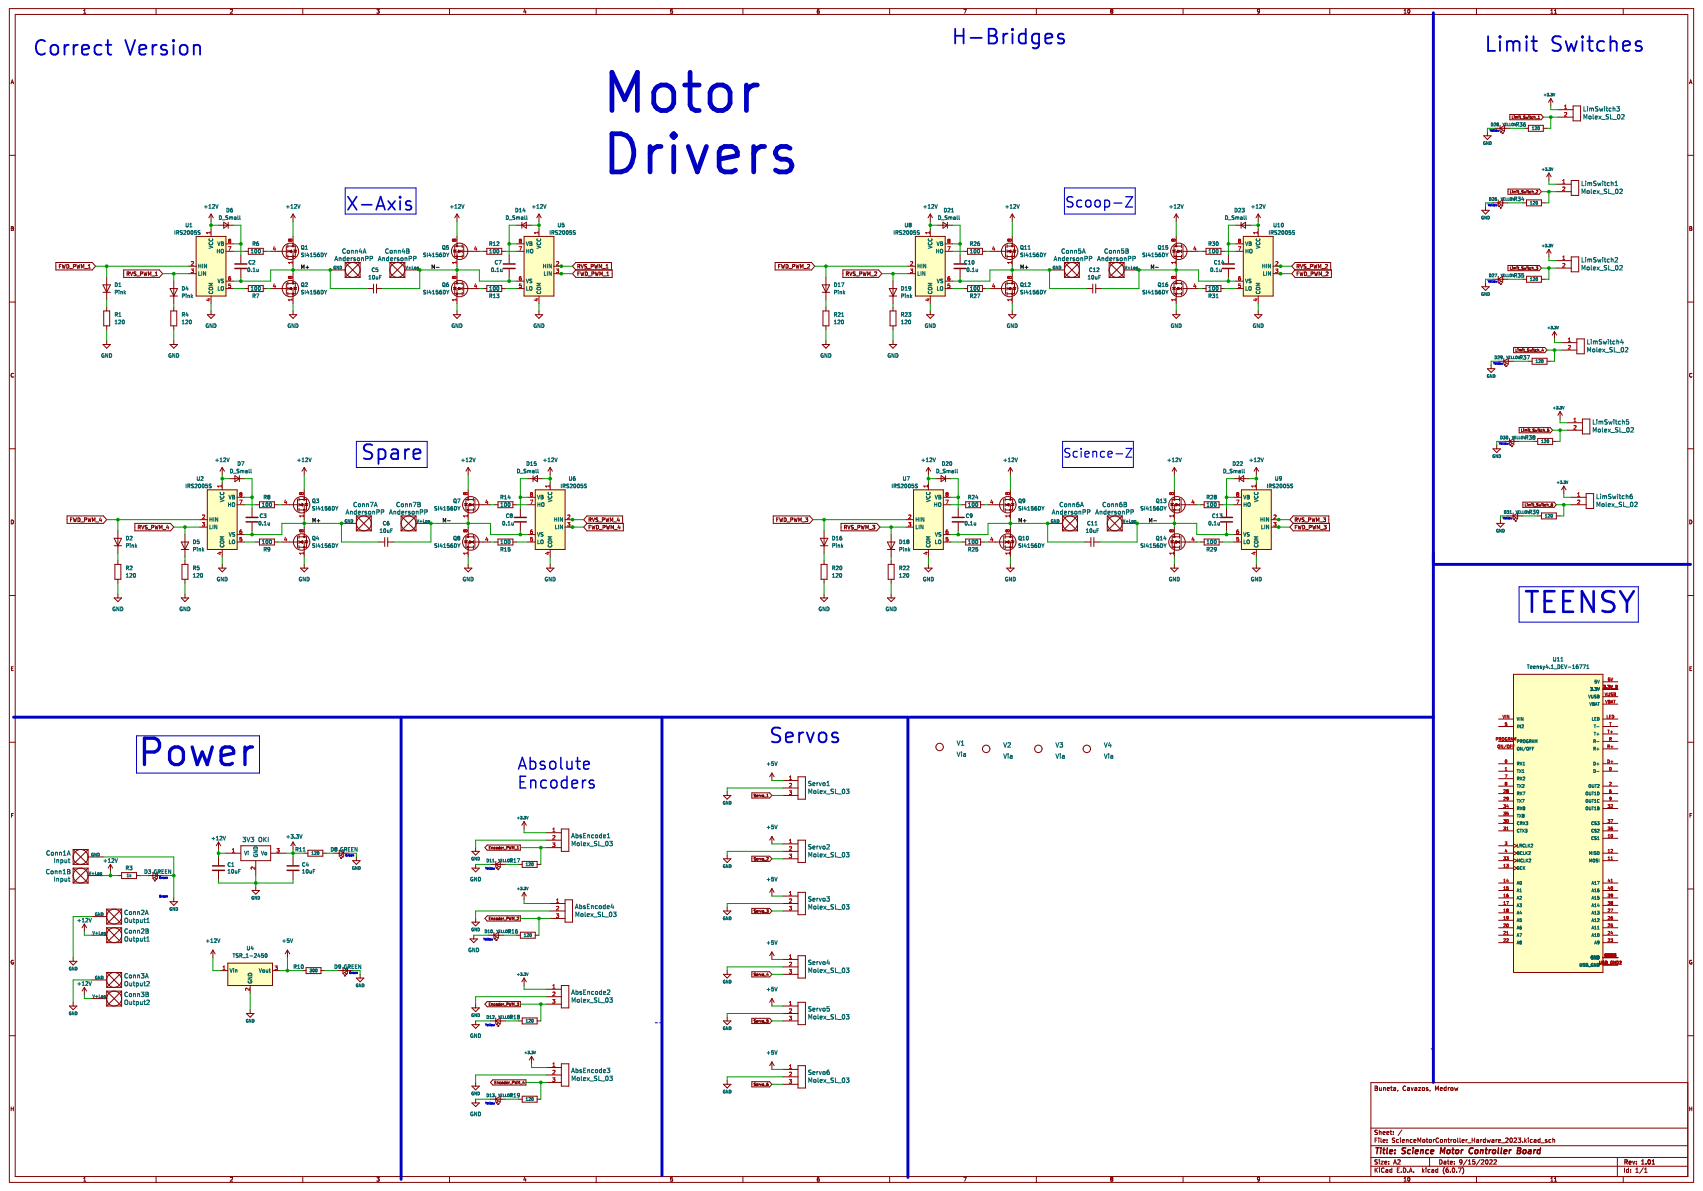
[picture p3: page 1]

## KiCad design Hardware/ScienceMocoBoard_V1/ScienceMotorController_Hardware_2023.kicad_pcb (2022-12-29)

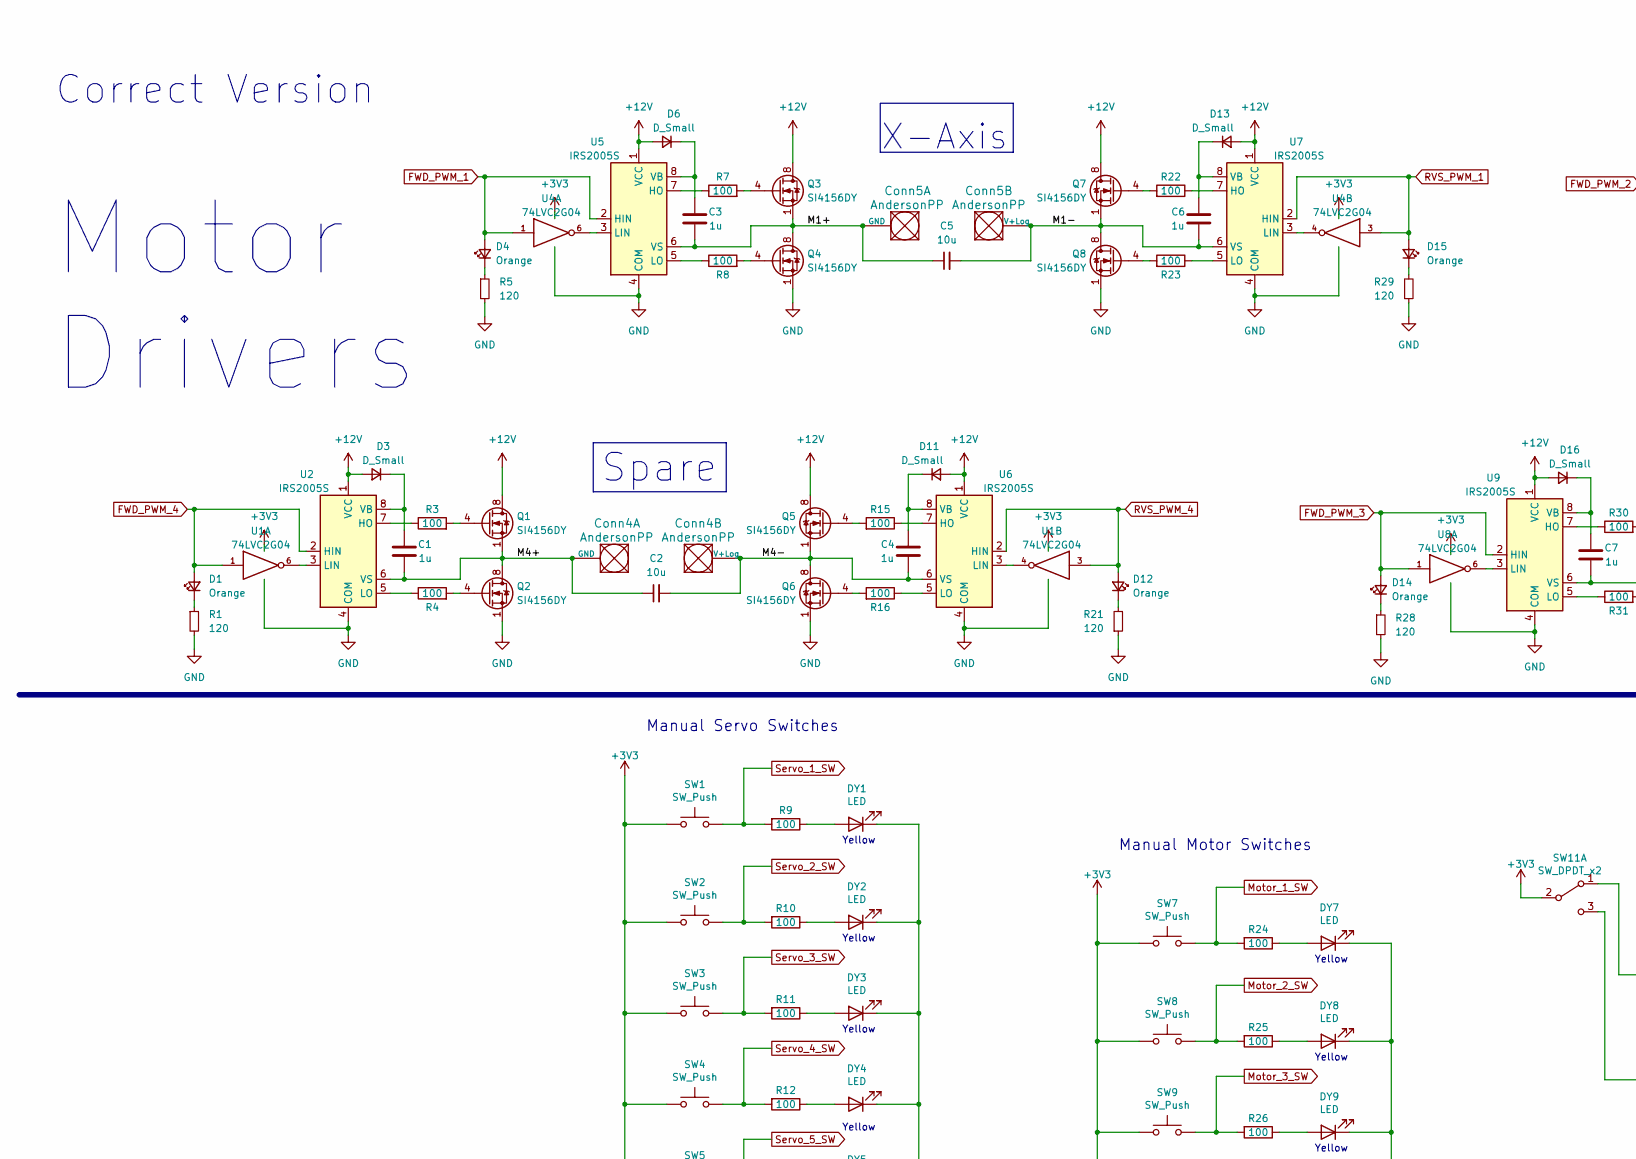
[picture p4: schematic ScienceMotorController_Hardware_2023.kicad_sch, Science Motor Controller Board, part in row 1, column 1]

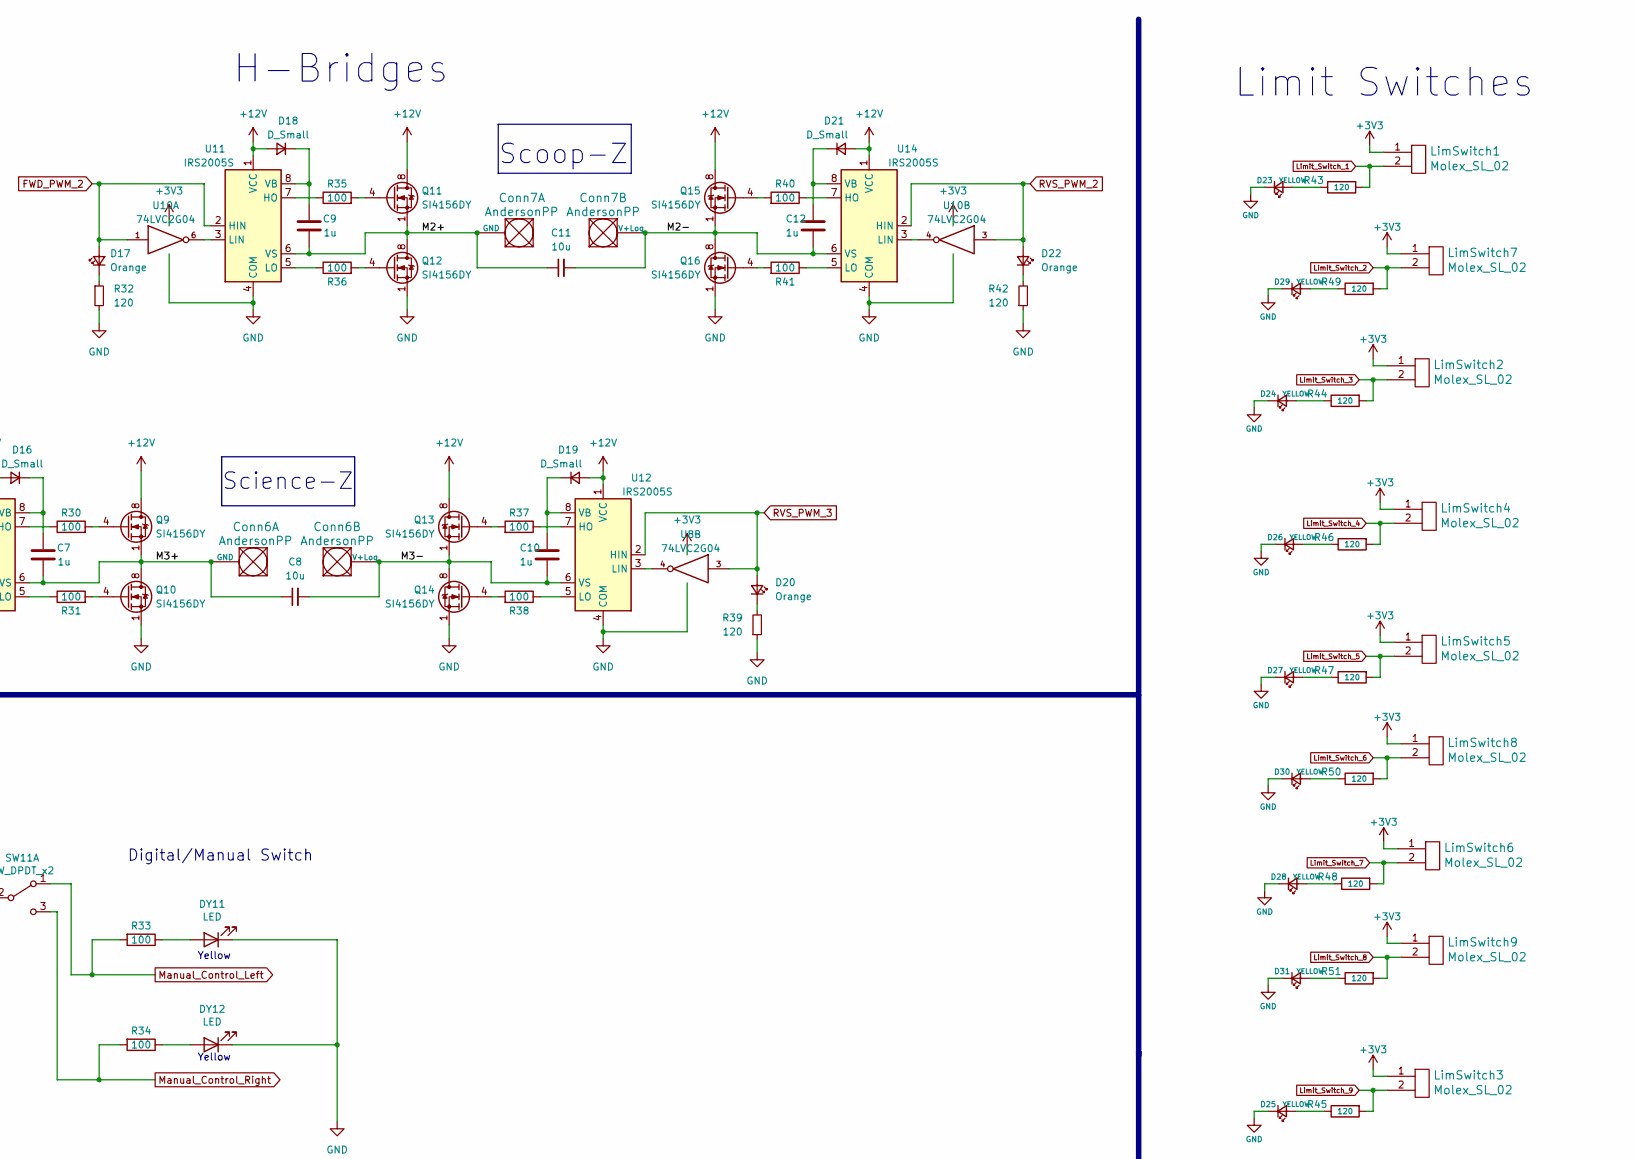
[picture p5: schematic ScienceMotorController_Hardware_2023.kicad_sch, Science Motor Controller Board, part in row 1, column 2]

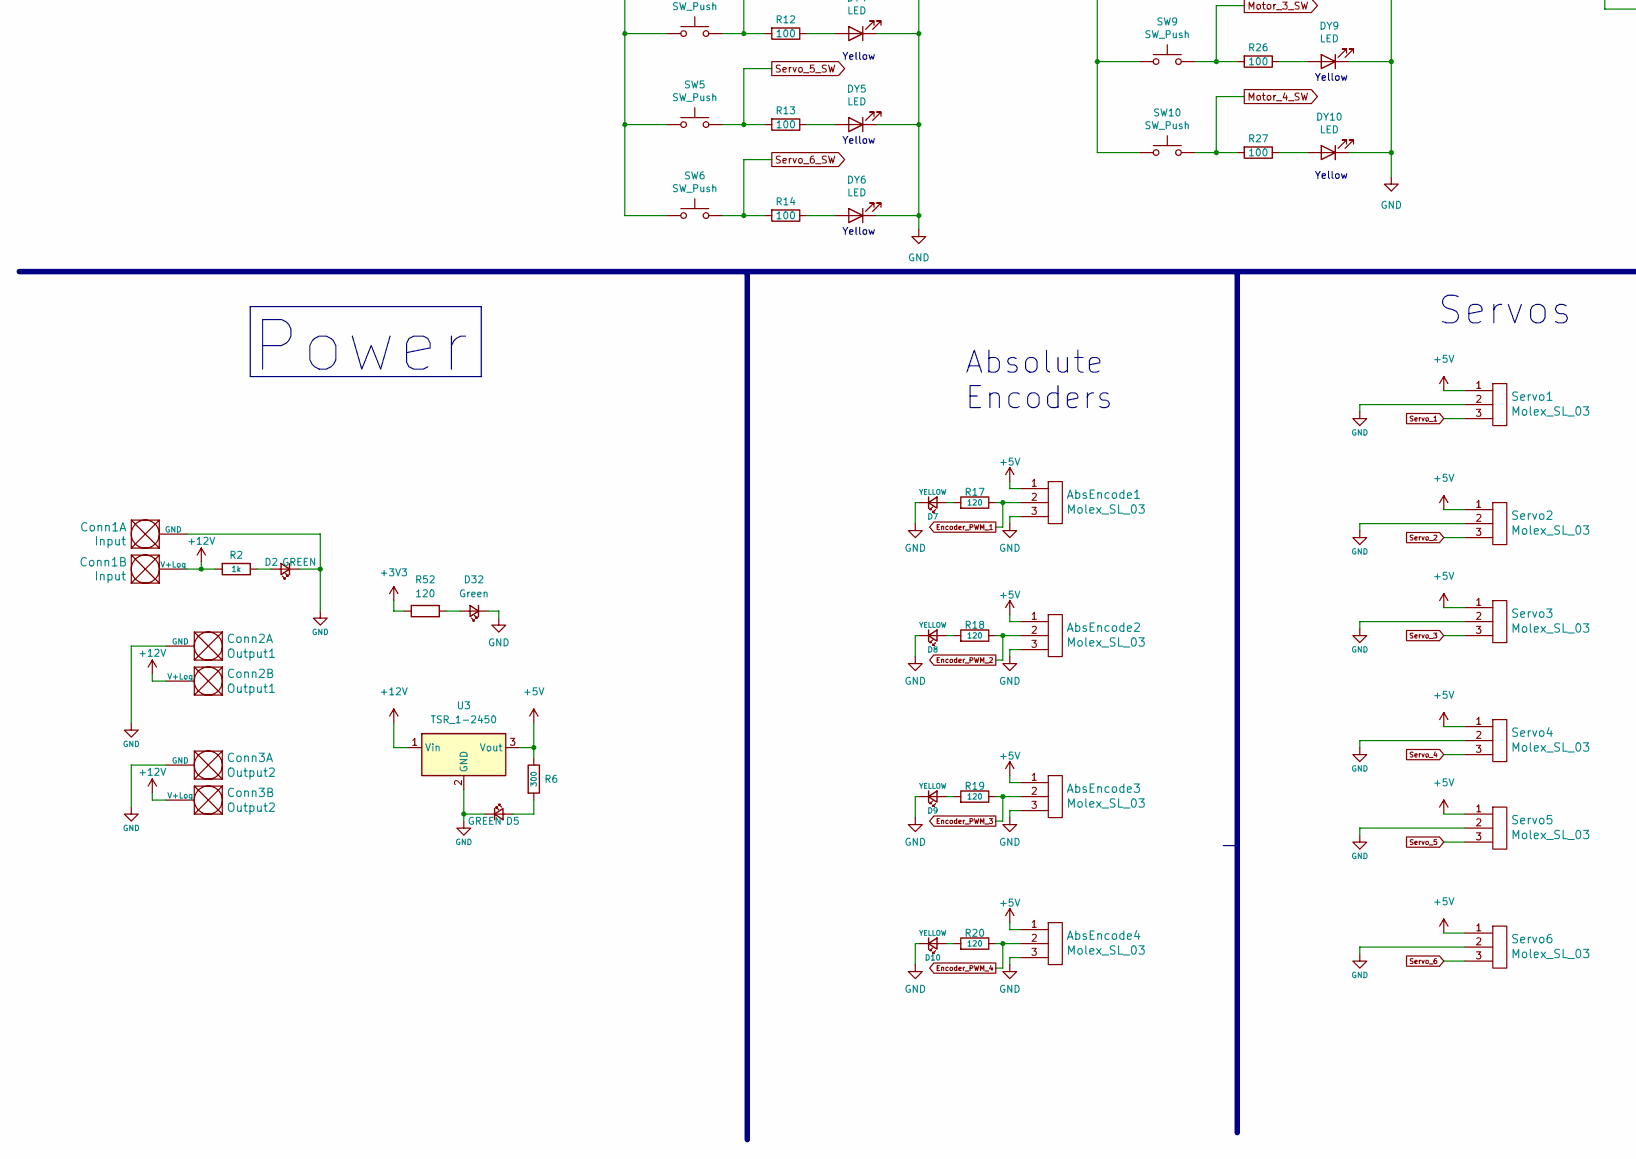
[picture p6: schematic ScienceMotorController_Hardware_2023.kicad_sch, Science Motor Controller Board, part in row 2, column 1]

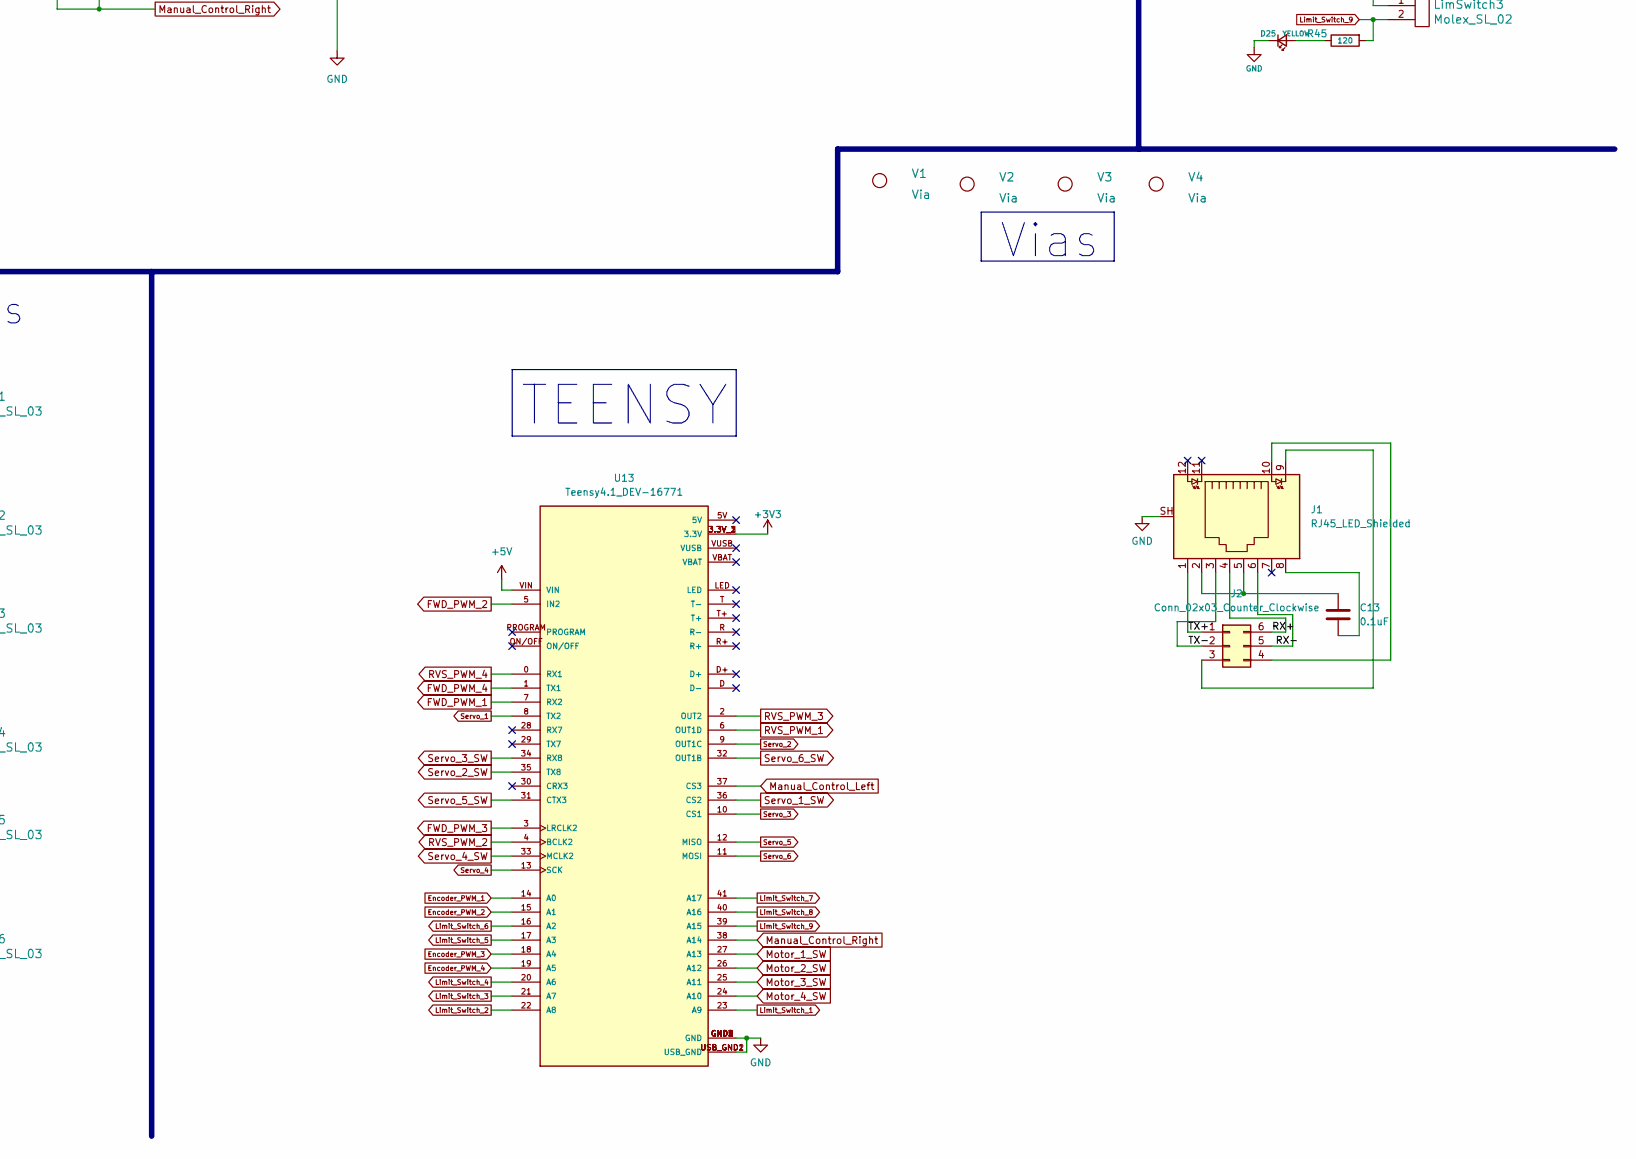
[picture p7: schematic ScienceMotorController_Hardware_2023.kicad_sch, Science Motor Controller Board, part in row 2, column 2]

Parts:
AbsEncode1, AbsEncode2, AbsEncode3, AbsEncode4: Molex_SL_03; MOLEX_SL_03_Vertical
C1, C3, C4, C6, C7, C9, C10, C12: 1u; C_0603_1608Metric
C2, C5, C8, C11: 10u; C_0603_1608Metric
C13: 0.1uF; C_0603_1608Metric_Pad1.08x0.95mm_HandSolder
Conn1: Input; Square_Anderson_2_H_Side_By_Side
Conn2: Output1; Square_Anderson_2_H_Side_By_Side
Conn3: Output2; Square_Anderson_2_H_Side_By_Side
Conn4, Conn5, Conn6, Conn7: AndersonPP; Square_Anderson_2_H_Side_By_Side
D1, D4, D12, D14, D15, D17, D20, D22: Orange; LED_0603_1608Metric_Pad1.05x0.95mm_HandSolder
D2, D5: GREEN; LED_0603_1608Metric_Pad1.05x0.95mm_HandSolder
D3, D6, D11, D13, D16, D18, D19, D21: D_Small; LED_0603_1608Metric_Pad1.05x0.95mm_HandSolder
D7, D8, D9, D10, D23, D24, D25, D26, D27, D28, D29, D30, D31: YELLOW; LED_0603_1608Metric_Pad1.05x0.95mm_HandSolder
D32: Green; LED_0603_1608Metric_Pad1.05x0.95mm_HandSolder
DY1, DY2, DY3, DY4, DY5, DY6, DY7, DY8, DY9, DY10, DY11, DY12: LED; LED_0603_1608Metric_Pad1.05x0.95mm_HandSolder
J1: RJ45_LED_Shielded; RJ45_Teensy
J2: Conn_02x03_Counter_Clockwise; PinHeader_2x03_P2.00mm_Vertical
LimSwitch1, LimSwitch2, LimSwitch3, LimSwitch4, LimSwitch5, LimSwitch6, LimSwitch7, LimSwitch8, LimSwitch9: Molex_SL_02; MOLEX_SL_02_Vertical
Q1, Q2, Q3, Q4, Q5, Q6, Q7, Q8, Q9, Q10, Q11, Q12, Q13, Q14, Q15, Q16: SI4156DY; SOIC-8_3.9x4.9mm_P1.27mm
R1, R5, R17, R18, R19, R20, R21, R28, R29, R32, R39, R42, R43, R44, R45, R46, R47, R48, R49, R50, R51, R52: 120; R_0603_1608Metric_Pad0.98x0.95mm_HandSolder
R2: 1k; R_0603_1608Metric_Pad0.98x0.95mm_HandSolder
R3, R4, R7, R8, R9, R10, R11, R12, R13, R14, R15, R16, R22, R23, R24, R25, R26, R27, R30, R31, R33, R34, R35, R36, R37, R38, R40, R41: 100; R_0603_1608Metric_Pad0.98x0.95mm_HandSolder
R6: 300; R_0603_1608Metric_Pad0.98x0.95mm_HandSolder
SW1, SW2, SW3, SW4, SW5, SW6, SW7, SW8, SW9, SW10: SW_Push; SW_SPST_EVPBF
SW11: SW_DPDT_x2; SW_Slide_1P2T_CK_OS102011MS2Q
Servo1, Servo2, Servo3, Servo4, Servo5, Servo6: Molex_SL_03; MOLEX_SL_03_Vertical
U1, U4, U8, U10: 74LVC2G04; SOT-23-6_Handsoldering
U2, U5, U6, U7, U9, U11, U12, U14: IRS2005S; SOIC-8_3.9x4.9mm_P1.27mm
U3: TSR_1-2450; Converter_DCDC_TRACO_TSR-1_THT
U13: Teensy4.1_DEV-16771; Teensy_4_1_Bare; PARTREV 4.1
V1, V2, V3, V4: Via; 4_40_Hole_Corner

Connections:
+3V3: LimSwitch1.1, LimSwitch2.1, LimSwitch3.1, LimSwitch4.1, LimSwitch5.1, LimSwitch6.1, LimSwitch7.1, LimSwitch8.1, LimSwitch9.1, R52.1, SW1.2, SW2.1, SW3.1, SW4.1, SW5.1, SW6.1, SW7.2, SW8.1, SW9.1, SW10.1, SW11.2 (B), U1.5 (VCC), U4.5 (VCC), U8.5 (VCC), U10.5 (VCC), U13.3.3V_1 (3.3V), U13.3.3V_2 (3.3V), U13.3.3V_3 (3.3V)
+5V: AbsEncode1.1, AbsEncode2.1, AbsEncode3.1, AbsEncode4.1, R6.1, Servo1.1, Servo2.1, Servo3.1, Servo4.1, Servo5.1, Servo6.1, U3.3 (Vout), U13.VIN
+12V: Conn1.2 (V+Log), Conn2.2 (V+Log), Conn3.2 (V+Log), D3.2 (A), D6.2 (A), D11.2 (A), D13.2 (A), D16.2 (A), D18.2 (A), D19.2 (A), D21.2 (A), Q1.5 (D), Q1.6 (D), Q1.7 (D), Q1.8 (D), Q3.5 (D), Q3.6 (D), Q3.7 (D), Q3.8 (D), Q5.5 (D), Q5.6 (D), Q5.7 (D), Q5.8 (D), Q7.5 (D), Q7.6 (D), Q7.7 (D), Q7.8 (D), Q9.5 (D), Q9.6 (D), Q9.7 (D), Q9.8 (D), Q11.5 (D), Q11.6 (D), Q11.7 (D), Q11.8 (D), Q13.5 (D), Q13.6 (D), Q13.7 (D), Q13.8 (D), Q15.5 (D), Q15.6 (D), Q15.7 (D), Q15.8 (D), R2.2, U2.1 (VCC), U3.1 (Vin), U5.1 (VCC), U6.1 (VCC), U7.1 (VCC), U9.1 (VCC), U11.1 (VCC), U12.1 (VCC), U14.1 (VCC)
/M1+: C3.2, C5.1, Conn5.1 (GND), Q3.1 (S), Q3.2 (S), Q3.3 (S), Q4.5 (D), Q4.6 (D), Q4.7 (D), Q4.8 (D), U5.6 (VS)
/M1-: C5.2, C6.2, Conn5.2 (V+Log), Q7.1 (S), Q7.2 (S), Q7.3 (S), Q8.5 (D), Q8.6 (D), Q8.7 (D), Q8.8 (D), U7.6 (VS)
/M2+: C9.2, C11.1, Conn7.1 (GND), Q11.1 (S), Q11.2 (S), Q11.3 (S), Q12.5 (D), Q12.6 (D), Q12.7 (D), Q12.8 (D), U11.6 (VS)
/M2-: C11.2, C12.2, Conn7.2 (V+Log), Q15.1 (S), Q15.2 (S), Q15.3 (S), Q16.5 (D), Q16.6 (D), Q16.7 (D), Q16.8 (D), U14.6 (VS)
/M3+: C7.2, C8.1, Conn6.1 (GND), Q9.1 (S), Q9.2 (S), Q9.3 (S), Q10.5 (D), Q10.6 (D), Q10.7 (D), Q10.8 (D), U9.6 (VS)
/M3-: C8.2, C10.2, Conn6.2 (V+Log), Q13.1 (S), Q13.2 (S), Q13.3 (S), Q14.5 (D), Q14.6 (D), Q14.7 (D), Q14.8 (D), U12.6 (VS)
/M4+: C1.2, C2.1, Conn4.1 (GND), Q1.1 (S), Q1.2 (S), Q1.3 (S), Q2.5 (D), Q2.6 (D), Q2.7 (D), Q2.8 (D), U2.6 (VS)
/M4-: C2.2, C4.2, Conn4.2 (V+Log), Q5.1 (S), Q5.2 (S), Q5.3 (S), Q6.5 (D), Q6.6 (D), Q6.7 (D), Q6.8 (D), U6.6 (VS)
/RX+: J1.4, J2.6
/RX-: J1.6, J2.5
/TX+: J1.1, J2.1
/TX-: J1.3, J2.2
Encoder_PWM_1: AbsEncode1.2, R17.1, U13.14 (A0)
Encoder_PWM_2: AbsEncode2.2, R18.1, U13.15 (A1)
Encoder_PWM_3: AbsEncode3.2, R19.1, U13.18 (A4)
Encoder_PWM_4: AbsEncode4.2, R20.1, U13.19 (A5)
FWD_PWM_1: D4.2 (A), U4.1, U5.2 (HIN), U13.7 (RX2)
FWD_PWM_2: D17.2 (A), U10.1, U11.2 (HIN), U13.5 (IN2)
FWD_PWM_3: D14.2 (A), U8.1, U9.2 (HIN), U13.3 (LRCLK2)
FWD_PWM_4: D1.2 (A), U1.1, U2.2 (HIN), U13.1 (TX1)
GND: AbsEncode1.3, AbsEncode2.3, AbsEncode3.3, AbsEncode4.3, Conn1.1 (GND), Conn2.1 (GND), Conn3.1 (GND), D2.1 (K), D5.1 (K), D7.1 (K), D8.1 (K), D9.1 (K), D10.1 (K), D23.1 (K), D24.1 (K), D25.1 (K), D26.1 (K), D27.1 (K), D28.1 (K), D29.1 (K), D30.1 (K), D31.1 (K), D32.1 (K), DY1.1 (K), DY2.1 (K), DY3.1 (K), DY4.1 (K), DY5.1 (K), DY6.1 (K), DY7.1 (K), DY8.1 (K), DY9.1 (K), DY10.1 (K), DY11.1 (K), DY12.1 (K), J1.SH, Q2.1 (S), Q2.2 (S), Q2.3 (S), Q4.1 (S), Q4.2 (S), Q4.3 (S), Q6.1 (S), Q6.2 (S), Q6.3 (S), Q8.1 (S), Q8.2 (S), Q8.3 (S), Q10.1 (S), Q10.2 (S), Q10.3 (S), Q12.1 (S), Q12.2 (S), Q12.3 (S), Q14.1 (S), Q14.2 (S), Q14.3 (S), Q16.1 (S), Q16.2 (S), Q16.3 (S), R1.2, R5.2, R21.1, R28.2, R29.1, R32.2, R39.1, R42.1, Servo1.2, Servo2.2, Servo3.2, Servo4.2, Servo5.2, Servo6.2, U1.2 (GND), U2.4 (COM), U3.2 (GND), U4.2 (GND), U5.4 (COM), U6.4 (COM), U7.4 (COM), U8.2 (GND), U9.4 (COM), U10.2 (GND), U11.4 (COM), U12.4 (COM), U13.GND1 (GND), U13.GND2 (GND), U13.GND3 (GND), U13.GND4 (GND), U13.GND5 (GND), U13.USB_GND1 (USB_GND), U13.USB_GND2 (USB_GND), U14.4 (COM)
Limit_Switch_1: LimSwitch1.2, R43.2, U13.23 (A9)
Limit_Switch_2: LimSwitch7.2, R49.2, U13.22 (A8)
Limit_Switch_3: LimSwitch2.2, R44.2, U13.21 (A7)
Limit_Switch_4: LimSwitch4.2, R46.2, U13.20 (A6)
Limit_Switch_5: LimSwitch5.2, R47.2, U13.17 (A3)
Limit_Switch_6: LimSwitch8.2, R50.2, U13.16 (A2)
Limit_Switch_7: LimSwitch6.2, R48.2, U13.41 (A17)
Limit_Switch_8: LimSwitch9.2, R51.2, U13.40 (A16)
Limit_Switch_9: LimSwitch3.2, R45.2, U13.39 (A15)
Manual_Control_Left: R33.2, SW11.1 (A), U13.37 (CS3)
Manual_Control_Right: R34.2, SW11.3 (C), U13.38 (A14)
Motor_1_SW: R24.2, SW7.1, U13.27 (A13)
Motor_2_SW: R25.2, SW8.2, U13.26 (A12)
Motor_3_SW: R26.2, SW9.2, U13.25 (A11)
Motor_4_SW: R27.2, SW10.2, U13.24 (A10)
unnamed: C1.1, D3.1 (K), U2.8 (VB)
unnamed: C3.1, D6.1 (K), U5.8 (VB)
unnamed: C4.1, D11.1 (K), U6.8 (VB)
unnamed: C6.1, D13.1 (K), U7.8 (VB)
unnamed: C7.1, D16.1 (K), U9.8 (VB)
unnamed: C9.1, D18.1 (K), U11.8 (VB)
unnamed: C10.1, D19.1 (K), U12.8 (VB)
unnamed: C12.1, D21.1 (K), U14.8 (VB)
unnamed: C13.1, J1.2, J1.5
unnamed: C13.2, J1.8
unnamed: D1.1 (K), R1.1
unnamed: D2.2 (A), R2.1
unnamed: D4.1 (K), R5.1
unnamed: D5.2 (A), R6.2
unnamed: D7.2 (A), R17.2
unnamed: D8.2 (A), R18.2
unnamed: D9.2 (A), R19.2
unnamed: D10.2 (A), R20.2
unnamed: D12.1 (K), R21.2
unnamed: D14.1 (K), R28.1
unnamed: D15.1 (K), R29.2
unnamed: D17.1 (K), R32.1
unnamed: D20.1 (K), R39.2
unnamed: D22.1 (K), R42.2
unnamed: D23.2 (A), R43.1
unnamed: D24.2 (A), R44.1
unnamed: D25.2 (A), R45.1
unnamed: D26.2 (A), R46.1
unnamed: D27.2 (A), R47.1
unnamed: D28.2 (A), R48.1
unnamed: D29.2 (A), R49.1
unnamed: D30.2 (A), R50.1
unnamed: D31.2 (A), R51.1
unnamed: D32.2 (A), R52.2
unnamed: DY1.2 (A), R9.1
unnamed: DY2.2 (A), R10.1
unnamed: DY3.2 (A), R11.1
unnamed: DY4.2 (A), R12.1
unnamed: DY5.2 (A), R13.1
unnamed: DY6.2 (A), R14.1
unnamed: DY7.2 (A), R24.1
unnamed: DY8.2 (A), R25.1
unnamed: DY9.2 (A), R26.1
unnamed: DY10.2 (A), R27.1
unnamed: DY11.2 (A), R33.1
unnamed: DY12.2 (A), R34.1
unnamed: J1.9, J2.3
unnamed: J1.10, J2.4
unnamed: Q1.4 (G), R3.2
unnamed: Q2.4 (G), R4.2
unnamed: Q3.4 (G), R7.2
unnamed: Q4.4 (G), R8.2
unnamed: Q5.4 (G), R15.2
unnamed: Q6.4 (G), R16.2
unnamed: Q7.4 (G), R22.2
unnamed: Q8.4 (G), R23.2
unnamed: Q9.4 (G), R30.2
unnamed: Q10.4 (G), R31.2
unnamed: Q11.4 (G), R35.2
unnamed: Q12.4 (G), R36.2
unnamed: Q13.4 (G), R37.2
unnamed: Q14.4 (G), R38.2
unnamed: Q15.4 (G), R40.2
unnamed: Q16.4 (G), R41.2
unnamed: R3.1, U2.7 (HO)
unnamed: R4.1, U2.5 (LO)
unnamed: R7.1, U5.7 (HO)
unnamed: R8.1, U5.5 (LO)
unnamed: R15.1, U6.7 (HO)
unnamed: R16.1, U6.5 (LO)
unnamed: R22.1, U7.7 (HO)
unnamed: R23.1, U7.5 (LO)
unnamed: R30.1, U9.7 (HO)
unnamed: R31.1, U9.5 (LO)
unnamed: R35.1, U11.7 (HO)
unnamed: R36.1, U11.5 (LO)
unnamed: R37.1, U12.7 (HO)
unnamed: R38.1, U12.5 (LO)
unnamed: R40.1, U14.7 (HO)
unnamed: R41.1, U14.5 (LO)
unnamed: U1.4, U6.3 (LIN)
unnamed: U1.6, U2.3 (LIN)
unnamed: U4.4, U7.3 (LIN)
unnamed: U4.6, U5.3 (LIN)
unnamed: U8.6, U9.3 (LIN)
unnamed: U10.4, U14.3 (LIN)
unnamed: U10.6, U11.3 (LIN)
unnamed: U8.4, U12.3 (LIN)
RVS_PWM_1: D15.2 (A), U4.3, U7.2 (HIN), U13.6 (OUT1D)
RVS_PWM_2: D22.2 (A), U10.3, U13.4 (BCLK2), U14.2 (HIN)
RVS_PWM_3: D20.2 (A), U8.3, U12.2 (HIN), U13.2 (OUT2)
RVS_PWM_4: D12.2 (A), U1.3, U6.2 (HIN), U13.0 (RX1)
Servo_1: Servo1.3, U13.8 (TX2)
Servo_1_SW: R9.2, SW1.1, U13.36 (CS2)
Servo_2: Servo2.3, U13.9 (OUT1C)
Servo_2_SW: R10.2, SW2.2, U13.35 (TX8)
Servo_3: Servo3.3, U13.10 (CS1)
Servo_3_SW: R11.2, SW3.2, U13.34 (RX8)
Servo_4: Servo4.3, U13.13 (SCK)
Servo_4_SW: R12.2, SW4.2, U13.33 (MCLK2)
Servo_5: Servo5.3, U13.12 (MISO)
Servo_5_SW: R13.2, SW5.2, U13.31 (CTX3)
Servo_6: Servo6.3, U13.11 (MOSI)
Servo_6_SW: R14.2, SW6.2, U13.32 (OUT1B)

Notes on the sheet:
Yellow
TEENSY
X-Axis
Power
Absolute Encoders
Motor Drivers
Vias
Spare
Correct Version
Manual Servo Switches
Limit Switches
Servos
Science-Z
Manual Motor Switches
H-Bridges
Scoop-Z
Digital/Manual Switch

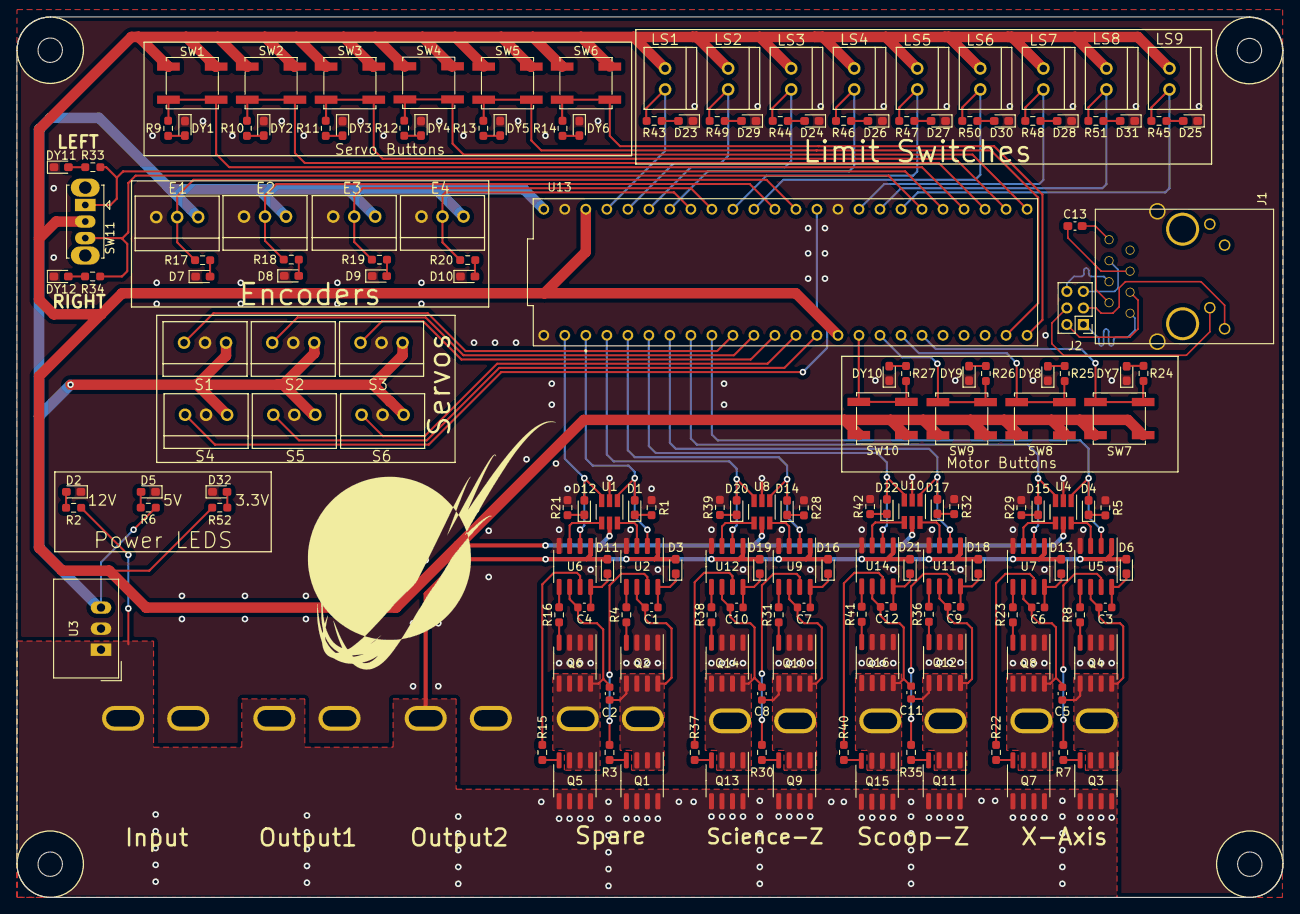
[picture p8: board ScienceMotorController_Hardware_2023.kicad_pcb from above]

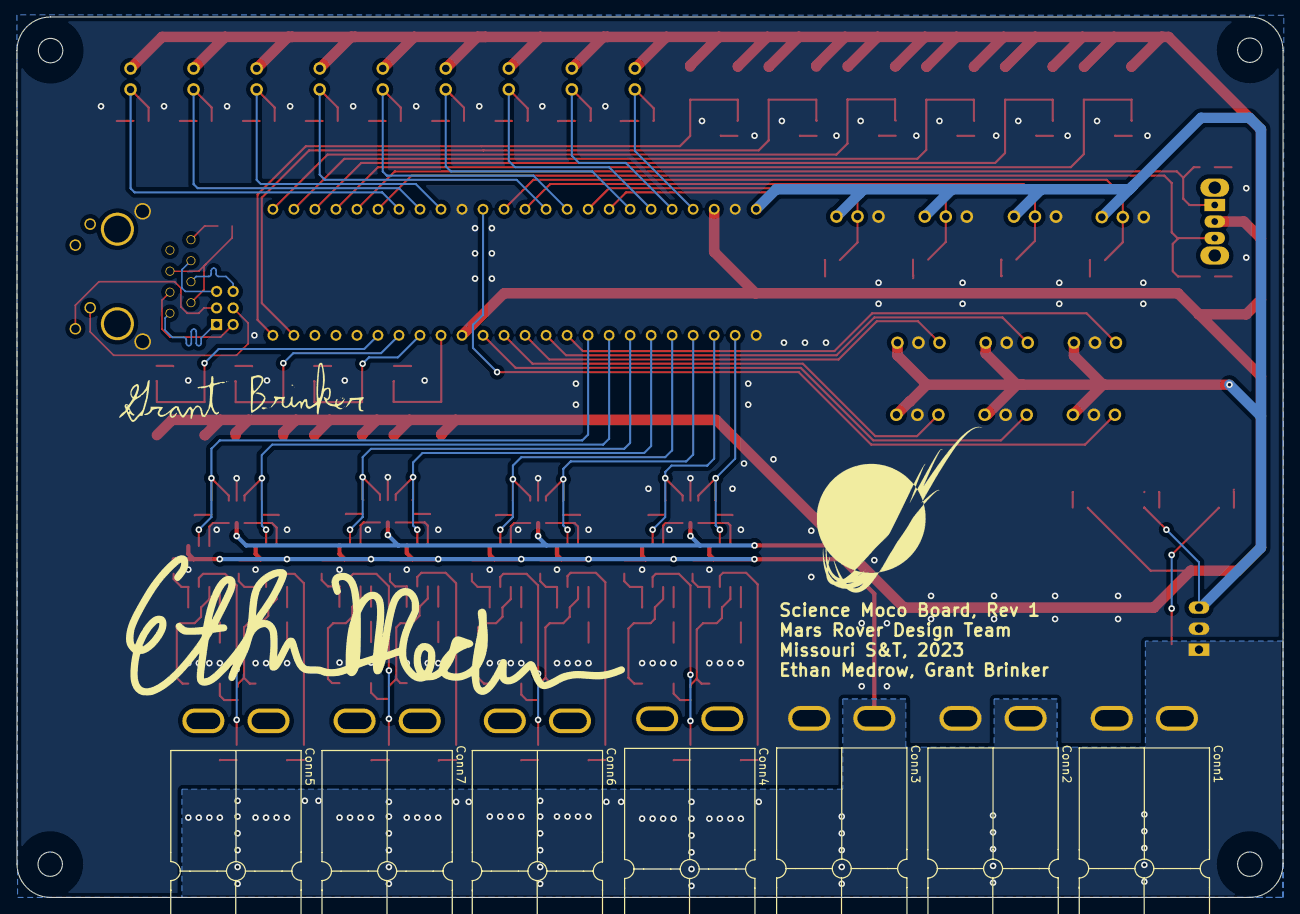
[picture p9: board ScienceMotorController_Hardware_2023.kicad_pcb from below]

Board: 2 copper layers, 153.0 x 106.4 mm, 182 parts (7 on the bottom side), 143 nets.

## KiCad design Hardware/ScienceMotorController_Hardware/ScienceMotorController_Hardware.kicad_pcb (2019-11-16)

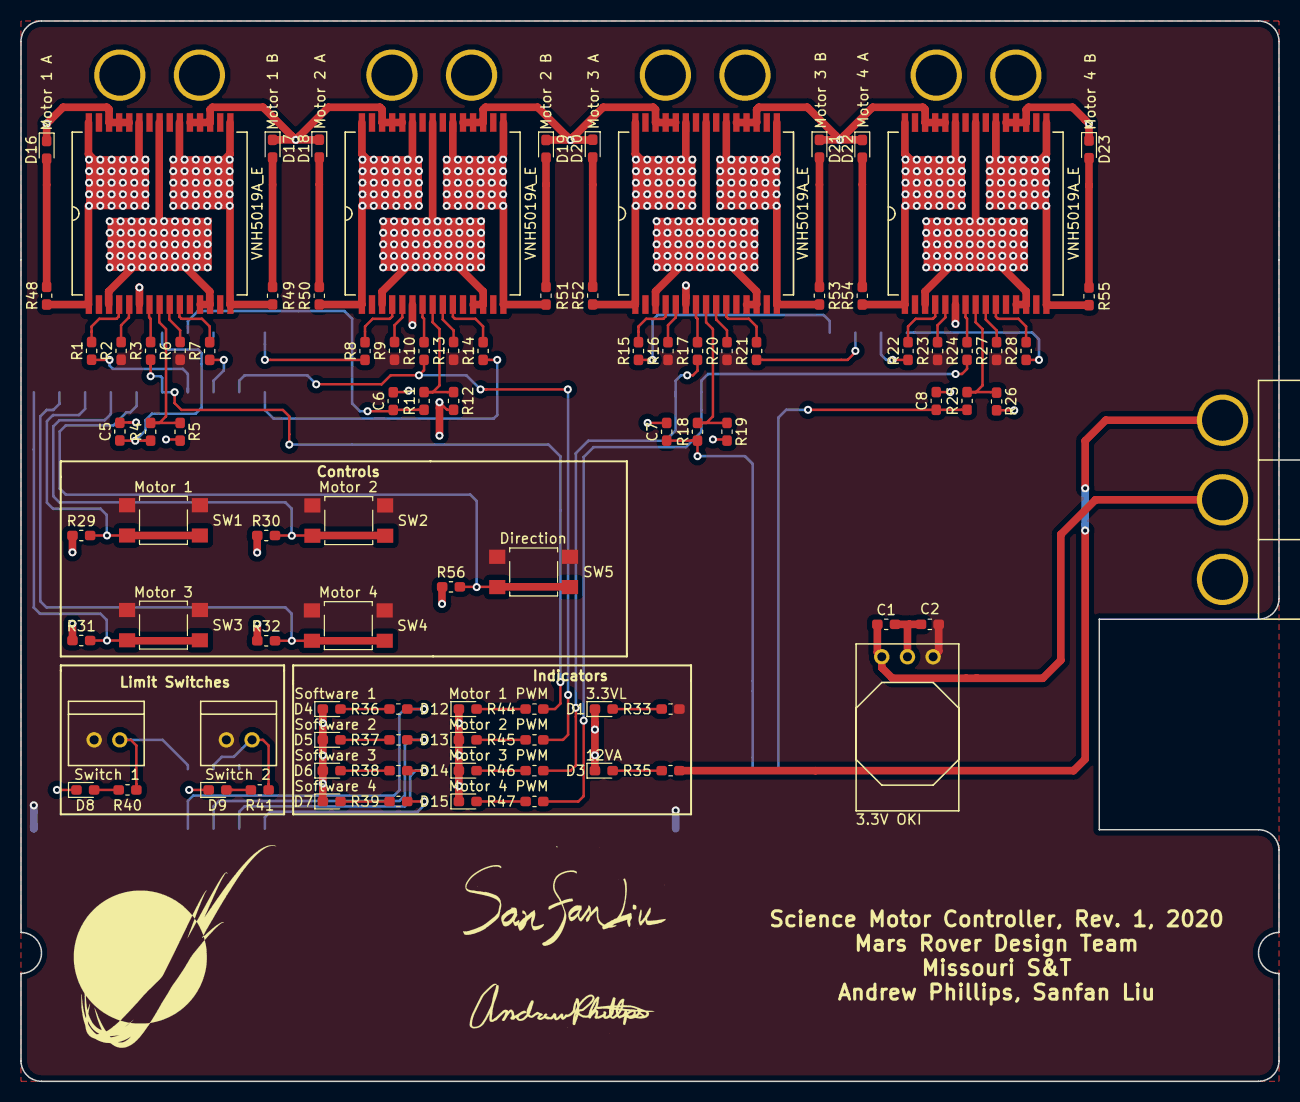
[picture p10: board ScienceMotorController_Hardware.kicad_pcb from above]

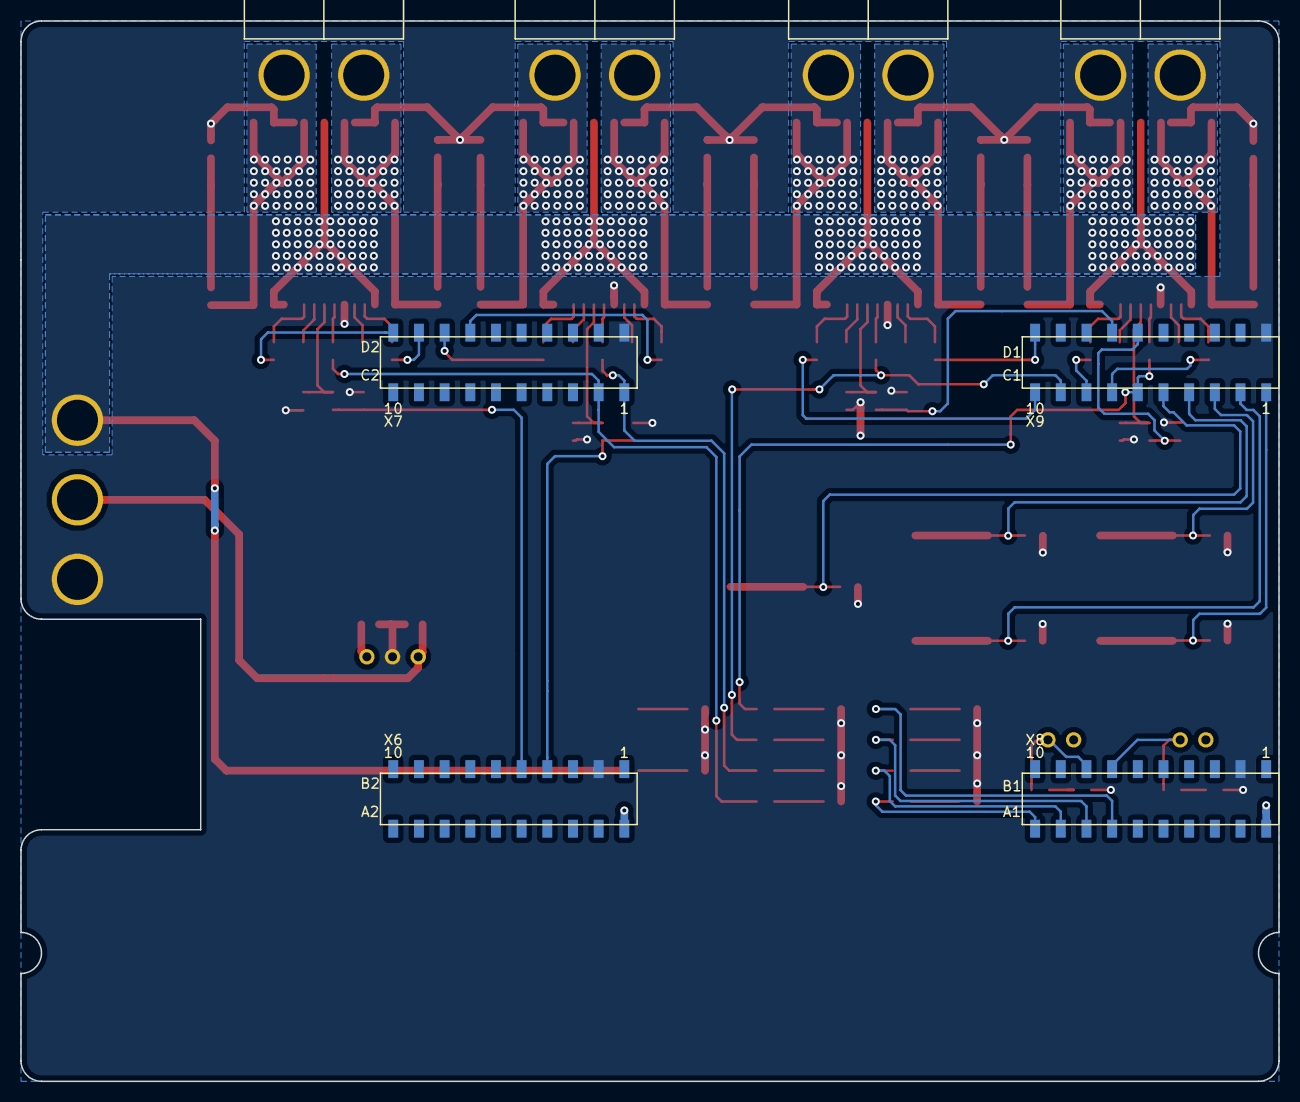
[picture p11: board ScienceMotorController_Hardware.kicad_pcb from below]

Board: 2 copper layers, 124.5 x 104.9 mm, 97 parts (4 on the bottom side), 83 nets.

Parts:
C1, C2: 10uF; C_0603_1608Metric_Pad1.05x0.95mm_HandSolder
C5, C6, C7, C8: 33nF; C_0603_1608Metric_Pad1.05x0.95mm_HandSolder
Conn1: AndersonPP; Anderson_3_Horizontal_Side_by_Side
Conn2, Conn3, Conn4, Conn5: AndersonPP; Anderson_2_Horizontal_Side_by_Side
Conn6, Conn7: Molex_SL_02; MOLEX_SL_02_Vertical
D1: 3.3V_LED; LED_0603_1608Metric_Pad1.05x0.95mm_HandSolder
D3: 12VA_LED; LED_0603_1608Metric_Pad1.05x0.95mm_HandSolder
D4: SW_IND_1_LED; LED_0603_1608Metric_Pad1.05x0.95mm_HandSolder
D5: SW_IND_2_LED; LED_0603_1608Metric_Pad1.05x0.95mm_HandSolder
D6: SW_IND_3_LED; LED_0603_1608Metric_Pad1.05x0.95mm_HandSolder
D7: SW_IND_4_LED; LED_0603_1608Metric_Pad1.05x0.95mm_HandSolder
D8: LS_1_LED; LED_0603_1608Metric_Pad1.05x0.95mm_HandSolder
D9: LS_2_LED; LED_0603_1608Metric_Pad1.05x0.95mm_HandSolder
D12: M1_PWM_LED; LED_0603_1608Metric_Pad1.05x0.95mm_HandSolder
D13: M2_PWM_LED; LED_0603_1608Metric_Pad1.05x0.95mm_HandSolder
D14: M3_PWM_LED; LED_0603_1608Metric_Pad1.05x0.95mm_HandSolder
D15: M4_PWM_LED; LED_0603_1608Metric_Pad1.05x0.95mm_HandSolder
D16: M1_OUT_A_LED; LED_0603_1608Metric_Pad1.05x0.95mm_HandSolder
D17: M1_OUT_B_LED; LED_0603_1608Metric_Pad1.05x0.95mm_HandSolder
D18: M2_OUT_A_LED; LED_0603_1608Metric_Pad1.05x0.95mm_HandSolder
D19: M2_OUT_B_LED; LED_0603_1608Metric_Pad1.05x0.95mm_HandSolder
D20: M3_OUT_A_LED; LED_0603_1608Metric_Pad1.05x0.95mm_HandSolder
D21: M3_OUT_B_LED; LED_0603_1608Metric_Pad1.05x0.95mm_HandSolder
D22: M4_OUT_A_LED; LED_0603_1608Metric_Pad1.05x0.95mm_HandSolder
D23: M4_OUT_B_LED; LED_0603_1608Metric_Pad1.05x0.95mm_HandSolder
R1, R3, R6, R7, R8, R10, R13, R14, R15, R17, R21, R22, R24, R28, R44, R45, R46, R47: 1K; R_0603_1608Metric_Pad1.05x0.95mm_HandSolder
R2, R9, R16, R20, R23, R27: 3.3K; R_0603_1608Metric_Pad1.05x0.95mm_HandSolder
R4, R11, R18, R25: 10K; R_0603_1608Metric_Pad1.05x0.95mm_HandSolder
R5, R12, R19, R26, R35, R48, R49, R50, R51, R52, R53, R54, R55: 1.5K; R_0603_1608Metric_Pad1.05x0.95mm_HandSolder
R29, R30, R31, R32, R33, R36, R37, R38, R39, R40, R41, R56: 500; R_0603_1608Metric_Pad1.05x0.95mm_HandSolder
SW1, SW2, SW3, SW4, SW5: SW_Push; SW_SPST_TL3305A
U1: TM4C129E_Launchpad; TM4C129E_Launchpad_FULL_SMD_BOTTOM
U2: 3.3V OKI; OKI_Horizontal
U4, U5, U6, U7: VNH5019A_E; MultiPowerSO_30

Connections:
+3V3: C2.1, Conn6.1, Conn7.1, R2.1, R6.1, R9.1, R13.1, R16.1, R20.1, R23.1, R27.1, R33.1, SW1.1, SW2.1, SW3.1, SW4.1, SW5.1, U1.+3V3, U1.+3V3', U2.3
+12L: C1.1, Conn1.2, U2.1
+12VA: Conn1.3, R35.1, U4.3, U4.12, U4.13, U4.23, U4.32, U5.3, U5.12, U5.13, U5.23, U5.32, U6.3, U6.12, U6.13, U6.23, U6.32, U7.3, U7.12, U7.13, U7.23, U7.32
GND: C1.2, C2.2, C5.2, C6.2, C7.2, C8.2, Conn1.1, D1.1, D3.1, D4.1, D5.1, D6.1, D7.1, D8.1, D9.1, D12.1, D13.1, D14.1, D15.1, D16.1, D17.1, D18.1, D19.1, D20.1, D21.1, D22.1, D23.1, R5.2, R12.2, R19.2, R26.2, R29.1, R30.1, R31.1, R32.1, R56.1, U1.GND, U2.2, U4.6, U4.18, U4.19, U4.20, U4.26, U4.27, U4.28, U5.6, U5.18, U5.19, U5.20, U5.26, U5.27, U5.28, U6.6, U6.18, U6.19, U6.20, U6.26, U6.27, U6.28, U7.6, U7.18, U7.19, U7.20, U7.26, U7.27, U7.28
LS_1: Conn6.2, R40.1, U1.PD7
LS_2: Conn7.2, R41.1, U1.PA6
M1_CS: C5.1, R4.1, U1.PD1
M1_IN_A: R1.1, U1.PL0
M1_IN_B: R7.1, U1.PL1
M1_OUT_A: Conn2.1, R48.1, U4.1, U4.25, U4.30, U4.31
M1_OUT_B: Conn2.2, R49.1, U4.15, U4.16, U4.21, U4.33
M1_PWM: R3.1, R44.2, U1.PL5
M2_CS: C6.1, R11.1, U1.PD0
M2_IN_A: R8.1, U1.PP2
M2_IN_B: R14.1, U1.PL3
M2_OUT_A: Conn3.1, R50.1, U5.1, U5.25, U5.30, U5.31
M2_OUT_B: Conn3.2, R51.1, U5.15, U5.16, U5.21, U5.33
M2_PWM: R10.1, R45.2, U1.PL2
M3_CS: C7.1, R18.1, U1.PB5
M3_IN_A: R15.1, U1.PQ3
M3_IN_B: R21.1, U1.PP3
M3_OUT_A: Conn4.1, R52.1, U6.1, U6.25, U6.30, U6.31
M3_OUT_B: Conn4.2, R53.1, U6.15, U6.16, U6.21, U6.33
M3_PWM: R17.1, R46.2, U1.PG1
M4_CS: C8.1, R25.1, U1.PK0
M4_IN_A: R22.1, U1.PQ1
M4_IN_B: R28.1, U1.PM6
M4_OUT_A: Conn5.1, R54.1, U7.1, U7.25, U7.30, U7.31
M4_OUT_B: Conn5.2, R55.1, U7.15, U7.16, U7.21, U7.33
M4_PWM: R24.1, R47.2, U1.PK4
MSW_1: R29.2, SW1.2, U1.PF3
MSW_2: R30.2, SW2.2, U1.PG0
MSW_3: R31.2, SW3.2, U1.PF1
MSW_4: R32.2, SW4.2, U1.PF2
MSW_5: R56.2, SW5.2, U1.PL4
unnamed: D1.2, R33.2
unnamed: D3.2, R35.2
unnamed: D4.2, R36.2
unnamed: D5.2, R37.2
unnamed: D6.2, R38.2
unnamed: D7.2, R39.2
unnamed: D8.2, R40.2
unnamed: D9.2, R41.2
unnamed: D12.2, R44.1
unnamed: D13.2, R45.1
unnamed: D14.2, R46.1
unnamed: D15.2, R47.1
unnamed: D16.2, R48.2
unnamed: D17.2, R49.2
unnamed: D18.2, R50.2
unnamed: D19.2, R51.2
unnamed: D20.2, R52.2
unnamed: D21.2, R53.2
unnamed: D22.2, R54.2
unnamed: D23.2, R55.2
unnamed: R1.2, U4.4
unnamed: R2.2, U4.5
unnamed: R3.2, U4.7
unnamed: R4.2, R5.1, U4.8
unnamed: R6.2, U4.9
unnamed: R7.2, U4.10
unnamed: R8.2, U5.4
unnamed: R9.2, U5.5
unnamed: R10.2, U5.7
unnamed: R11.2, R12.1, U5.8
unnamed: R13.2, U5.9
unnamed: R14.2, U5.10
unnamed: R15.2, U6.4
unnamed: R16.2, U6.5
unnamed: R17.2, U6.7
unnamed: R18.2, R19.1, U6.8
unnamed: R20.2, U6.9
unnamed: R21.2, U6.10
unnamed: R22.2, U7.4
unnamed: R23.2, U7.5
unnamed: R24.2, U7.7
unnamed: R25.2, R26.1, U7.8
unnamed: R27.2, U7.9
unnamed: R28.2, U7.10
SW_IND_1: R36.1, U1.PD3
SW_IND_2: R37.1, U1.PC7
SW_IND_3: R38.1, U1.PB2
SW_IND_4: R39.1, U1.PB3

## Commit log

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2019-10-11 PCB High Level Layout
    Lacking some major traces such as power
    [ScienceMotorController_Hardware.kicad_pcb, ScienceMotorController_Hardware.sch]
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2019-10-12 Fixed Silkscreen
    [ScienceMotorController_Hardware.kicad_pcb]
2019-10-13 PDR Advice
    Removed 2 limit switches & relocated LS LEDs, added direction switch. Also relocated LS, Control, and Indicator blocks and revamped pin assignments to optimize traces.
    [ScienceMotorController_Hardware.kicad_pcb, ScienceMotorController_Hardware.sch]
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2019-10-13 Similar to PostPDR, but using 3V3 instead of 5V for VNH5019A-E
    [ScienceMotorController_Hardware.kicad_pcb, ScienceMotorController_Hardware.sch]
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2020-09-25 Placed Tiva headers, took note of which pins were PWM
    [ScienceMotorController02.sch]
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2020-10-09 changed everything to actuation, added schottky diode, added A/B flags to tiva
    [ScienceMotorController01.sch, ScienceMotorController02.sch, ScienceMotorController03.sch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]
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2020-10-28 fixed hierarchical
    [ScienceMotorController.sch, ScienceMotorController01.sch, ScienceMotorController02.sch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]
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2020-10-31 Fixed 3.3V, added encoders
    [ScienceMotorController.sch, ScienceMotorController01.sch, ScienceMotorController02.sch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]
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2020-11-15 fixed islands
    [ScienceMotorController.kicad_pcb]
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2020-11-30 cleaned up vias, widened planes, grounded more areas
    [ScienceMotorController.kicad_pcb]
2020-12-02 fixed that one trace
    [ScienceMotorController.kicad_pcb]
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2020-12-02 Fixed Gerbs and Step files
    [ScienceMotorController-B_Cu.gbr, ScienceMotorController-B_Mask.gbr, ScienceMotorController-B_Paste.gbr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]
2020-12-02 Fixed BOM mistakes
    [BOM.csv]
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2021-10-16 LED's, Servos, Power, and PWM pins?
    - Labeled LED's Green/Blue
    - Changed Resistor values for LED's
    - Changed Power so that there is an extra OKI converting power from 12V to 5V since the Servo's needed it
    - Added Servo's
    - Restructured sheet slightly
    - PDR gonna be a breeze
    [ScienceMotorController.sch]
2021-11-01 Schematic changes: Added 5V converter and Servos
    Schematic:
    -Added a 5V converter to the power section, connected to Power
    -Added Servos in their own section, altered TIVA to add servo connections
    [ScienceMotorController.sch]
2021-11-30 Finished Schematic
    -Changed Motor Controller Chips
    -Removed 2 Pumps
    -Removed 2 Limit Switches
    -Added 2 Absolute Encoders
    -Added 3 Solenoid Valves
    -Created Schematic Symbol and Footprint for Mosfet (footprint may need to be altered later)
    [ScienceMotorController-B_Cu.gbr, ScienceMotorController-B_Mask.gbr, ScienceMotorController-B_Paste.gbr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]
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2021-12-02 Created PCB and Put Close Components Near Each other
    [ScienceMotorController.kicad_pcb]
2021-12-03 Edge cuts, GND plane, a little more organized
    [ScienceMotorController.kicad_pcb, ScienceMotorController.sch]
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2021-12-04 Worked on patterns for SolValve, LimSwitch, OKIs, and Clock for PCB
    [ScienceMotorController.kicad_pcb, ScienceMotorController.sch]
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2021-12-04 Put New LimSwitch compoments next to eachother in PCB layout
    [ScienceMotorController.kicad_pcb]
2021-12-04 Bunch more traces, slightly fixed some schematic issues
    - LEDs on the solenoid valves were incorrectly labeled as "green".
    - The front plane of the board is now +12VA instead of ground
    [ScienceMotorController.kicad_pcb, ScienceMotorController.sch, ScienceMotorController.xml]
2021-12-04 Put components on the board and added some traces
    [ScienceMotorController.kicad_pcb, ScienceMotorController.sch]
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2021-12-12 modified: Hardware/ScienceMotorController/ScienceMotorController.kicad_pcb modified: Hardware/ScienceMotorController/ScienceMotorController.kicad_pcb-bak modified: Hardware/ScienceMotorController/Sci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
    [ScienceMotorController.kicad_pcb, ScienceMotorController.sch]
2021-12-12 created moco circuits
    Use the GND pin 25 on a 5mil grid with the entire circuit selected to move around
    [ScienceMotorController.kicad_pcb]
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2021-12-13 changed on oki to 5V actuation for servos, began making solenoid circuits
    [ScienceMotorController.kicad_pcb, ScienceMotorController.sch]
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2021-12-14 deleted extra LEDs and Resistors. Generated and loaded new netlist.
    [ScienceMotorController.kicad_pcb, ScienceMotorController.sch]
2021-12-14 more connections made, beginning to connect moco ICs
    [ScienceMotorController.kicad_pcb]
2021-12-14 resistors on moco chips added.
    Had changed netlist to try a different placement for the motor LEDs, but reverted to original position
    [ScienceMotorController.kicad_pcb, ScienceMotorController.sch]
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2021-12-15 connected 5V and osc. buses to moco ICs. Updated netlist to have pins closer to tiva pins
    [ScienceMotorController.kicad_pcb, ScienceMotorController.sch]
2021-12-15 continued connecting caps and resistors. Moved around some Tiva pins for the moco ICs
    [ScienceMotorController.kicad_pcb, ScienceMotorController.sch]
2021-12-15 began reworking moco IC control traces. Will need to rearrange the netlist to reduce complexity of traces
    [ScienceMotorController.kicad_pcb, ScienceMotorController.sch]
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2021-12-30 began fixing rescue libraries
    created ScienceMotorController.lib as the new project level library
    [ScienceMotorController.sch]
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2022-02-22 Changed Ground Plane for Motor Stalls
    [ScienceMotorController.kicad_pcb]
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2022-02-22 9 Solenoids, Fixed PWM Overlap
    [ScienceMotorController.kicad_pcb, ScienceMotorController.sch]
2022-02-25 Removed 5V Oki, Moved +12V Passthrough Trace, Added Zener Diodes for Current Sense
    [ScienceMotorController.kicad_pcb, ScienceMotorController.sch]
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2022-09-15 Modified PWM flags
    Modified PWM flags so orientation matched signal direction, also included whole Project along with generated BOM
    [ScienceMocoBoard_1.01.csv, ScienceMocoBoard_1.01.kicad_pcb, ScienceMocoBoard_1.01.kicad_sch]
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2022-10-11 Updated Motor Controllers
    Now has 7 motor controllers. Relabeled flags on MOCOs. Deleted solenoids. Need to add flags to TIVAs.
    [ScienceMotorController_Hardware_2023.kicad_sch]
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2022-10-18 Started Layout
    Update H-Bridges. Added Footprints. Started Layout with edge cuts and coopers.
    [ScienceMotorController_Hardware_2023.kicad_pcb, ScienceMotorController_Hardware_2023.kicad_sch]
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2022-10-29 Reworked Layout to be better
    [ScienceMotorController_Hardware_2023.kicad_pcb, ScienceMotorController_Hardware_2023.kicad_sch]
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2022-11-03 Power Plane Added, New Powerlines, Made Silkscreen Labels
    [ScienceMotorController_Hardware_2023.csv, ScienceMotorController_Hardware_2023.kicad_pcb, ScienceMotorController_Hardware_2023.xlsx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]
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2022-12-18 H-Bridges organized and on board. PCB components sorted.
    [ScienceMotorController_Hardware_2023.kicad_pcb, ScienceMotorController_Hardware_2023.kicad_sch]
2022-12-18 Fixed schematic
    [ScienceMotorController_Hardware_2023.kicad_sch]
2022-12-18 Fixed encoder connections
    [ScienceMotorController_Hardware_2023.kicad_sch]
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2022-12-20 Fixed trace + made STEP file
    [ScienceMotorController_Hardware_2023.kicad_pcb]
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2022-12-28 Fixed GND islands
    [ScienceMotorController_Hardware_2023.kicad_pcb]
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2022-12-29 Fixed power plane
    [ScienceMotorController_Hardware_2023.kicad_pcb]
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

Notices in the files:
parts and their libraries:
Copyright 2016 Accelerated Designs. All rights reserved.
